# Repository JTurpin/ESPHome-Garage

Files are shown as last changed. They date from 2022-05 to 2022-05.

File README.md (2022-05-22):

# ESPHome Based Garage Monitor

## Introduction
I built this circuit board to monitor my garage as well as control the garage door opener. This board is capable of reading door state through a switch, controlling the door, and using a BME680 to measure, temperature, humidity, volatile organic compounds (combustible gasses), and carbon dioxide.

## Hardware
Custom PCB created in Eagle CAD. I had these run at [seeedstudio-fusion](https://www.seeedstudio.com/fusion_pcb.html). The boards have been tested and are currently functioning in my garage.

## Interfacing with the garage door opener
There are inputs and outputs to read and control up to two doors. The ```DoorX-In``` are a simple digital read. I use magnetic reed switches that are normally open for this. They can be had cheaply as many alarm system used the for door and window sensors like [this](https://www.amazon.com/VictorsHome-Magnetic-Surface-Adhesive-Security/dp/B094XJ7K8K).

To controll the door simply run a 2 conductor wire from the ```DoorX`` screw terminals to the same terminals that the wall switch mounted inside the garage is connected to.

## Home Assistant Configuration
ESPHome needs to be installed and functioning:
1) Click on ```+ NEW DEVICE```
1) Click ```Continue```
2) Give it a name, I chose ```garage-monitor```
3) Select ```Pick specific board``` and ```Wemos D1 and Wemos D1 mini```
4) Select ```Skip```
5) Find the device and click ```EDIT```
6) Paste in the [yaml](ESPHome/garage-sensor.yaml) file and edit the proper wifi setting.
  
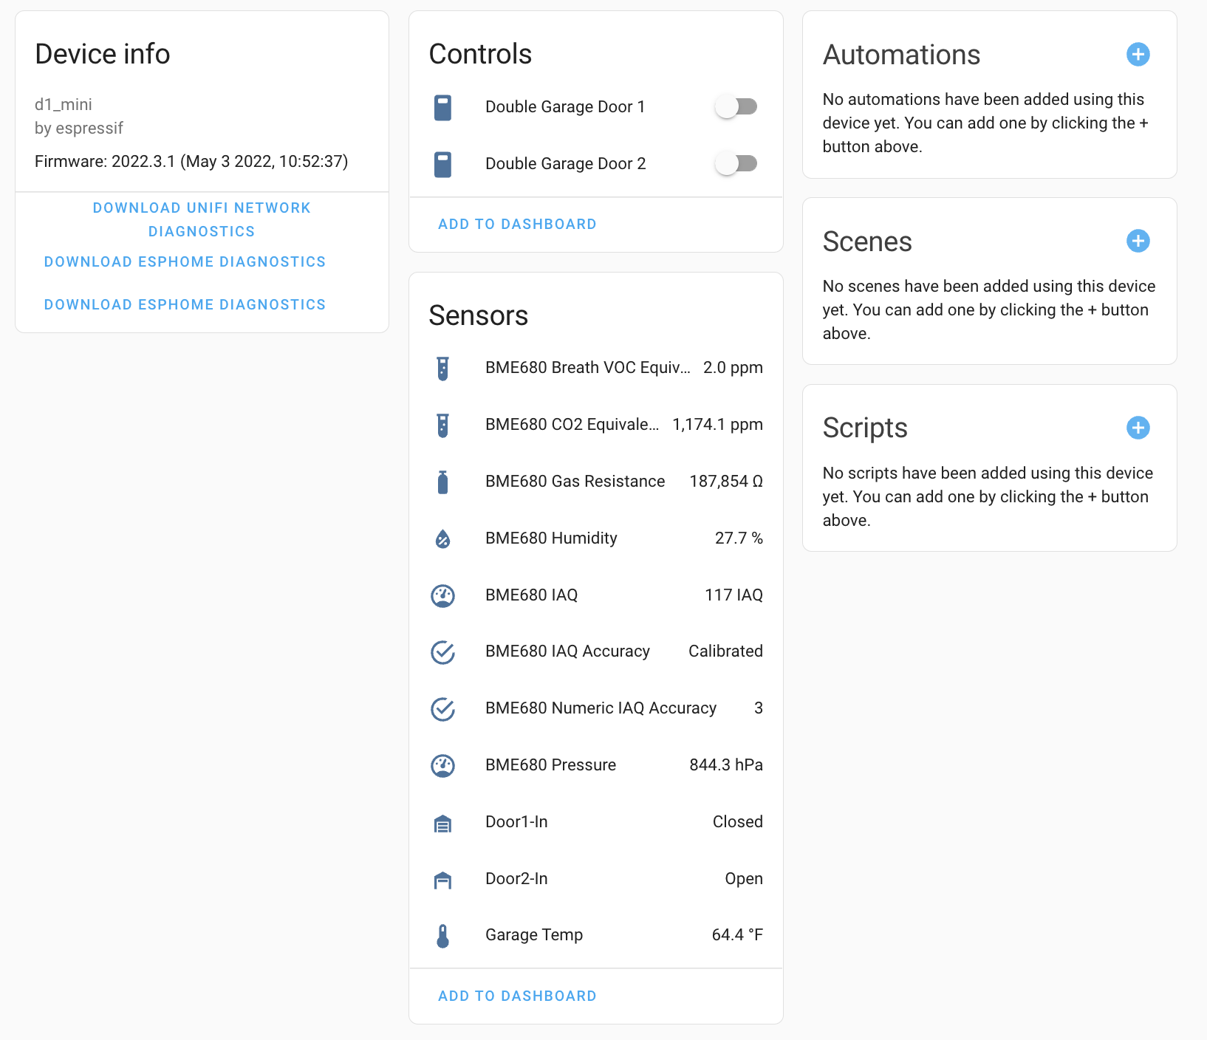
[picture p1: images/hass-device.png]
Home Assistant device view


## Automations
I use NodeRed to automate many aspects of my smart home. Here are a couple related to my garage to get you going.
- Notify via pushover if the garage door is open for 15 minutes [json](NodeRed%20Flows/notify-door-open.json) NodeRed
- Quick reset the output on the "button push" (There is probably a better way to do this but I found this to be effective) [json](NodeRed%20Flows/quick-trigger.json) NodeRed

## To Do...
There's two WS2812b on the board that I haven't found a use for yet, they could be used for a number of things though. examples:
- Countdown timer until autmoated shut of garage door
- Gauge estimates like [this](images/lovelace_gauge_segments.png) for Temp, VOC, Humidity, CO2.
- etc

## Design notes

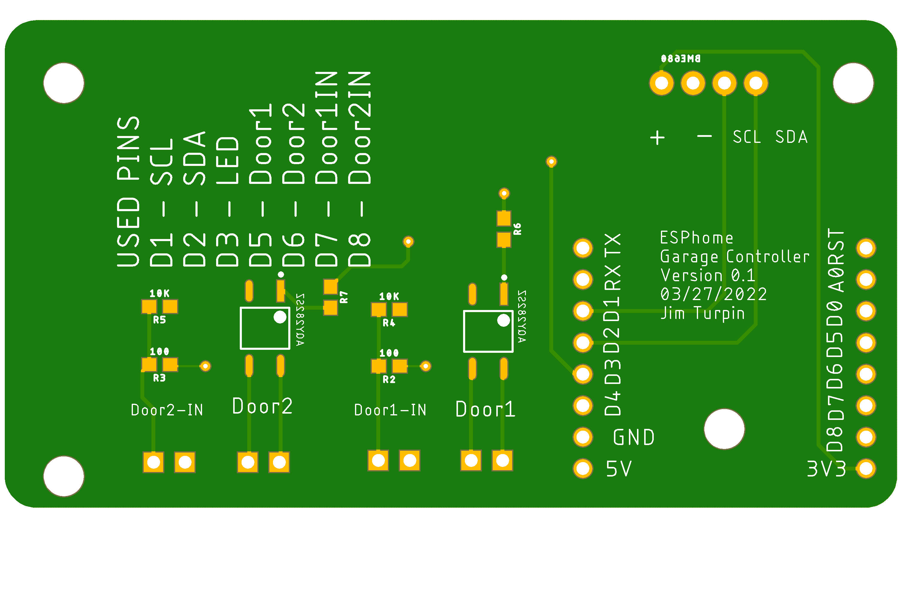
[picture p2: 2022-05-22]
images/PCB-bottom.png

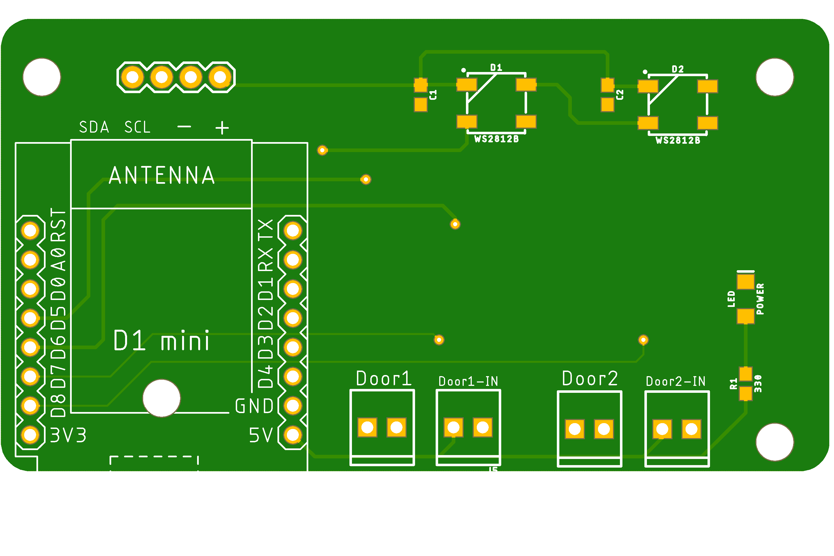
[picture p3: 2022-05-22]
images/PCB-top.png

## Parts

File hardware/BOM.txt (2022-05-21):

Partlist exported from Eagle

Part   Value         Device                               Package             Description                                                                                                     AMBIENT_TEMPERATURE_RANGE_HIGH AMBIENT_TEMPERATURE_RANGE_LOW AUTOMOTIVE CAPACITANCE CENTROID_NOT_SPECIFIED DATASHEET                                                          DEVICE_CLASS_L1   DEVICE_CLASS_L2 DEVICE_CLASS_L3    DIGIKEY_DESCRIPTION          DIGIKEY_PART_NUMBER FOOTPRINT_PARAMETERS_1                                                                                                                                                                                                                                                                                                                                                                                                                                                                                                                                                                                                                                                                                                                                                                                                                                                                                                                                                                                                                                                                                                                                                                                                                                                                                                                                                                                                                                                                                                                                                                                                                                                                                                                                                                                                                                                                                                                                                                                                                                                                                                                                                                                                                                                                                                                                                                                                                                                                                                                                                                                                                                                                                FOOTPRINT_PARAMETERS_2                                                                                                                                                                                                                                                                                                                                                                                                                                                                                                                                                                                                                                                                                                                                                                                                                                                                                                                                                                                                                                                                                                                                                                                                                                                                                                                                                                                                                                                                                                                                                                                                                                                                                                                                                                                                                                                                                                                                                                                                                                                                                                                                                                                                                                                                                                                                                                                                                                                                                                                                                                                                                                                                                FOOTPRINT_PARAMETERS_3                                                                                                                                                                                                                                                                                                                                                                                                                                                                                                                                                                                                                                                                                                                                                                                                                                                                                                                                                                                                                                                                                                                                                                                                                                                                                                                                                                                                                                                                                                                                                                                                                                                                                                                                                                                                                                                                                                                                                                                                                                                                                                                                                                                                                                                                                                                                                                                                                                                                                                                                                                                                                                                                                FOOTPRINT_VARIANT_NAME_0  FOOTPRINT_VARIANT_NAME_1 FOOTPRINT_VARIANT_NAME_2 FOOTPRINT_VARIANT_NAME_3 HEIGHT INPUT_CURRENT IPC_LAND_PATTERN_NAME ISOLATION_VOLTAGE LEAD_FREE MAX_JUNCTION_TEMP MF    MFG_PACKAGE_IDENT MFG_PACKAGE_IDENT_DATE MFG_PACKAGE_IDENT_REV MOUSER_DESCRIPTION                                          MOUSER_PART_NUMBER MPN        NUMBER_OF_CONTACTS ON_STATE_RESISTANCE OUTPUT_CURRENT OUTPUT_VOLTAGE PACKAGE PREFIX PROD_ID    ROHS STANDOFF_HEIGHT TEMPERATURE_RANGE_HIGH TEMPERATURE_RANGE_LOW THROW_CONFIGURATION VALUE   VERIFICATION_VERSION
C1     15pF          15PF-0603-50V-5%                     0603                15pF ceramic capacitors                                                                                                                                                                                                                                                                                                                                                                                                                                                                                                                                                                                                                                                                                                                                                                                                                                                                                                                                                                                                                                                                                                                                                                                                                                                                                                                                                                                                                                                                                                                                                                                                                                                                                                                                                                                                                                                                                                                                                                                                                                                                                                                                                                                                                                                                                                                                                                                                                                                                                                                                                                                                                                                                                                                                                                                                                                                                                                                                                                                                                                                                                                                                                                                                                                                                                                                                                                                                                                                                                                                                                                                                                                                                                                                                                                                                                                                                                                                                                                                                                                                                                                                                                                                                                                                                                                                                                                                                                                                                                                                                                                                                                                                                                                                                                                                                                                                                                                                                                                                                                                                                                                                                                                                                                                                                                                                                                                                                                                                                                                                                                                                                                                                                                                                                                                                                                                                                                                                                                                                                                                                                                                                                                                                                                                                                                                                                                                                                                                                                                                                                                                                                                                                                                                                                                                                                                                                                                                                                                                                                                                                                                                                                                                                                                                                                                                                                                                                                                                                                                                                                                                                                                                                                                                                                                                                                                                                                                                                                                                                                                                                                                                                                                                                                                                                                                                                                                                                                                                                                                                                                                                                                                                                                                                                                                                                                                                                                                                                                                CAP-07881                                                                                        15pF                        
C2     15pF          15PF-0603-50V-5%                     0603                15pF ceramic capacitors                                                                                                                                                                                                                                                                                                                                                                                                                                                                                                                                                                                                                                                                                                                                                                                                                                                                                                                                                                                                                                                                                                                                                                                                                                                                                                                                                                                                                                                                                                                                                                                                                                                                                                                                                                                                                                                                                                                                                                                                                                                                                                                                                                                                                                                                                                                                                                                                                                                                                                                                                                                                                                                                                                                                                                                                                                                                                                                                                                                                                                                                                                                                                                                                                                                                                                                                                                                                                                                                                                                                                                                                                                                                                                                                                                                                                                                                                                                                                                                                                                                                                                                                                                                                                                                                                                                                                                                                                                                                                                                                                                                                                                                                                                                                                                                                                                                                                                                                                                                                                                                                                                                                                                                                                                                                                                                                                                                                                                                                                                                                                                                                                                                                                                                                                                                                                                                                                                                                                                                                                                                                                                                                                                                                                                                                                                                                                                                                                                                                                                                                                                                                                                                                                                                                                                                                                                                                                                                                                                                                                                                                                                                                                                                                                                                                                                                                                                                                                                                                                                                                                                                                                                                                                                                                                                                                                                                                                                                                                                                                                                                                                                                                                                                                                                                                                                                                                                                                                                                                                                                                                                                                                                                                                                                                                                                                                                                                                                                                                CAP-07881                                                                                        15pF
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

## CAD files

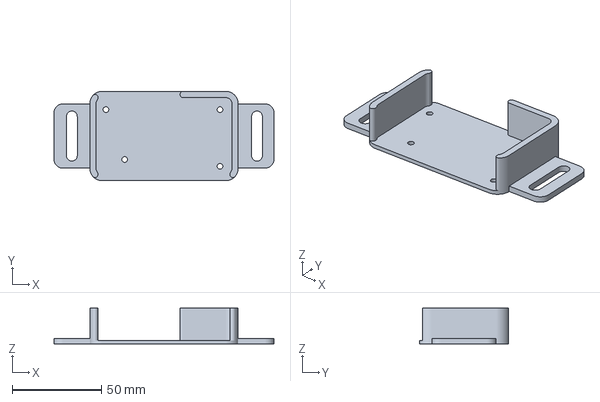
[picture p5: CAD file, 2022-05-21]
hardware/STL/ESPHome-Garage.3mf
123.0 x 50.0 x 20.0 mm

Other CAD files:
hardware/STL/ESPHome-Garage.f3d
hardware/STL/ESPHome-Garage.stl

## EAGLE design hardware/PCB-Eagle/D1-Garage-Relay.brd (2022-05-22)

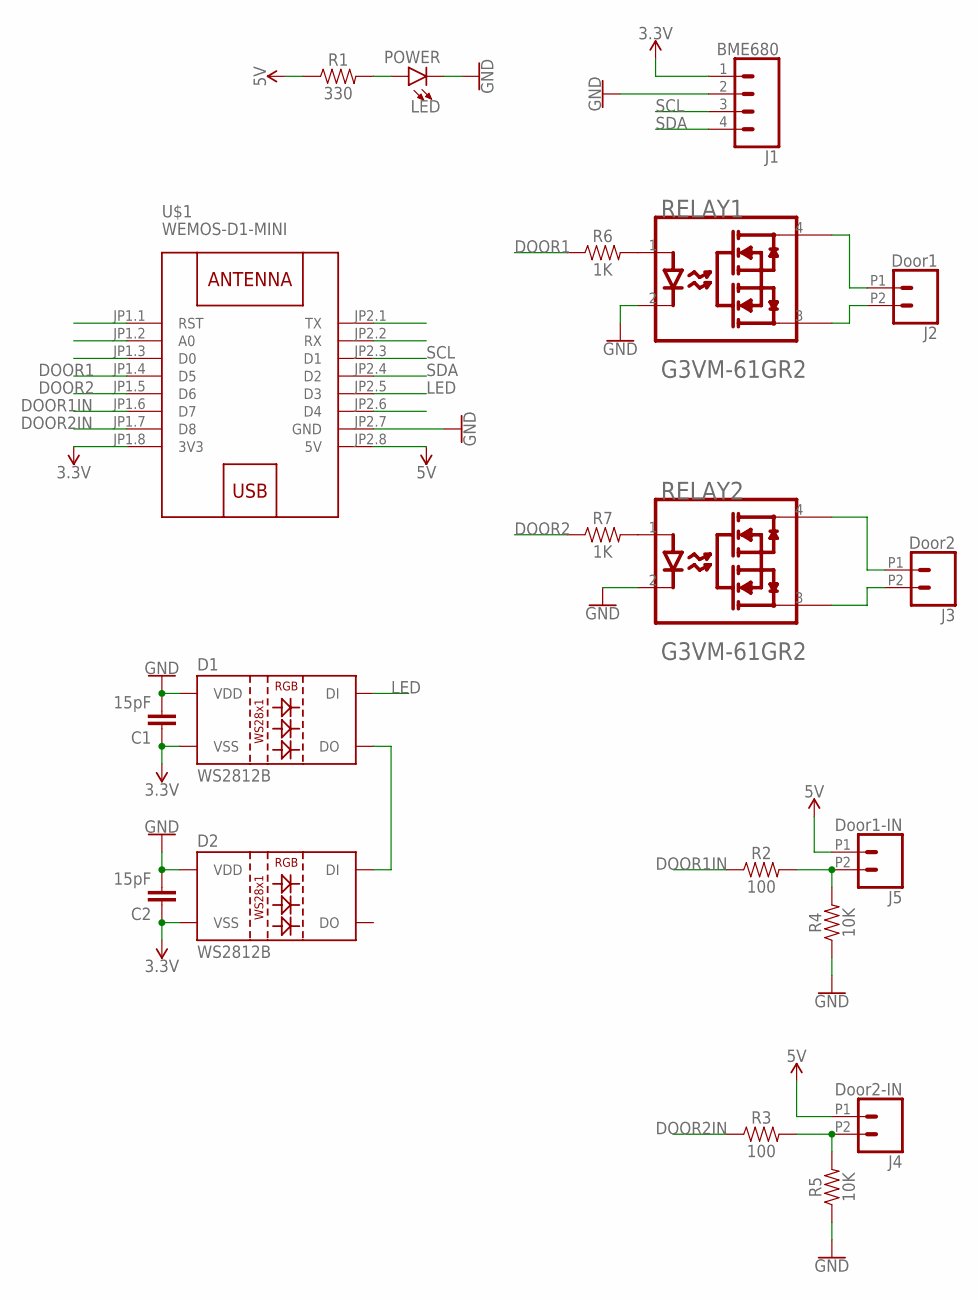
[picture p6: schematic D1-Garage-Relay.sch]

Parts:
C1, C2: 15pF; 0603
D1, D2: WS2812B
J1: BME680; 1X04
J2: Door1; 1X02_2.54_SCREWTERM
J3: Door2; 1X02_2.54_SCREWTERM
J4: Door2-IN; 1X02_2.54_SCREWTERM
J5: Door1-IN; 1X02_2.54_SCREWTERM
LED: POWER; LED-1206
R1: 330; 0603
R2, R3: 100; 0603
R4, R5: 10K; 0603
R6, R7: 1K; 0603
RELAY1, RELAY2: AQY282SZ; OMRON_G3VM-61GR2_3
U$1: WEMOS-D1-MINI

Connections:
3.3V: C1.1, C2.1, D1.3 (VSS), D2.3 (VSS), J1.1, U$1.JP1.8 (3V3)
5V: J4.P1 (1), J5.P1 (1), R1.1, U$1.JP2.8 (5V)
DOOR1: R6.1, U$1.JP1.4 (D5)
DOOR1IN: R2.1, U$1.JP1.6 (D7)
DOOR2: R7.1, U$1.JP1.5 (D6)
DOOR2IN: R3.1, U$1.JP1.7 (D8)
GND: C1.2, C2.2, D1.1 (VDD), D2.1 (VDD), J1.2, LED.C, R4.1, R5.1, RELAY1.2 (CATHODE), RELAY2.2 (CATHODE), U$1.JP2.7 (GND)
LED: D1.4 (DI), U$1.JP2.5 (D3)
unnamed: J2.P2 (2), RELAY1.3 (1_DRAIN)
unnamed: J3.P2 (2), RELAY2.3 (1_DRAIN)
unnamed: J2.P1 (1), RELAY1.4 (2_DRAIN)
unnamed: R6.2, RELAY1.1 (ANODE)
unnamed: J3.P1 (1), RELAY2.4 (2_DRAIN)
unnamed: R7.2, RELAY2.1 (ANODE)
unnamed: LED.A, R1.2
unnamed: J5.P2 (2), R2.2, R4.2
unnamed: J4.P2 (2), R3.2, R5.2
unnamed: D1.2 (DO), D2.4 (DI)
SCL: J1.3, U$1.JP2.3 (D1)
SDA: J1.4, U$1.JP2.4 (D2)

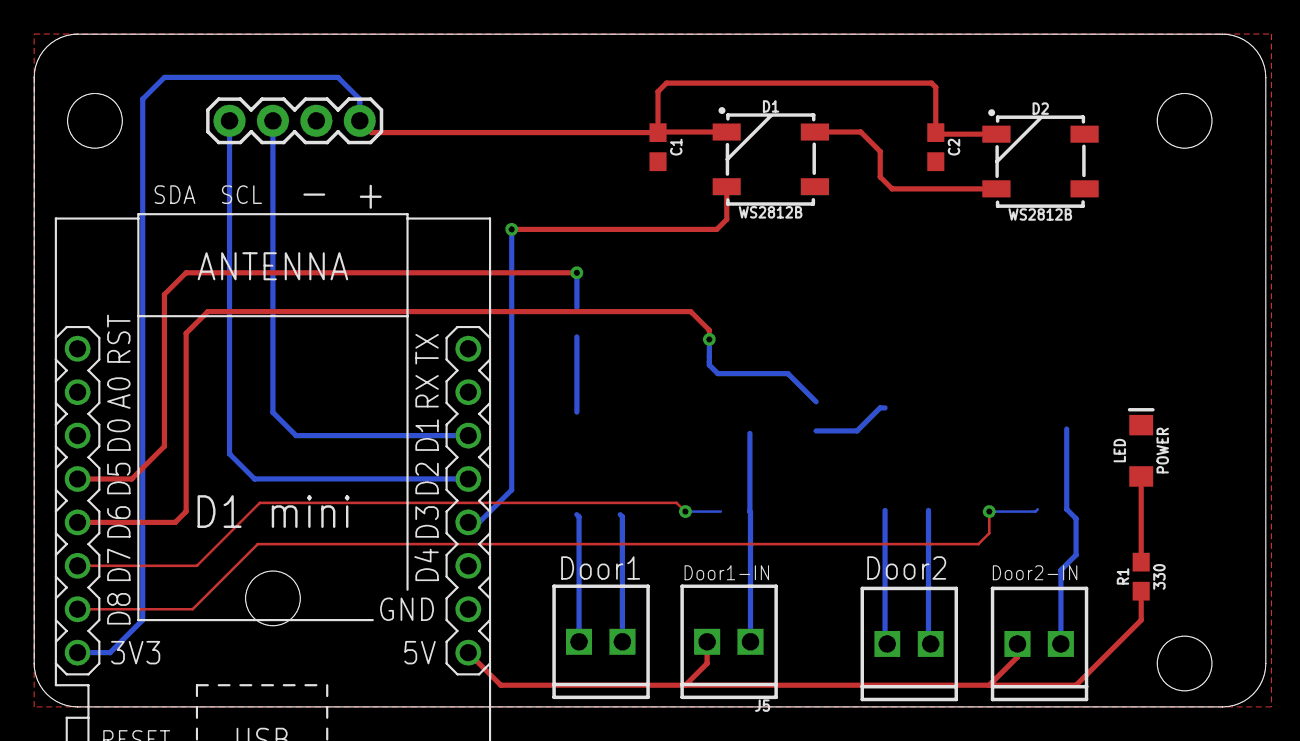
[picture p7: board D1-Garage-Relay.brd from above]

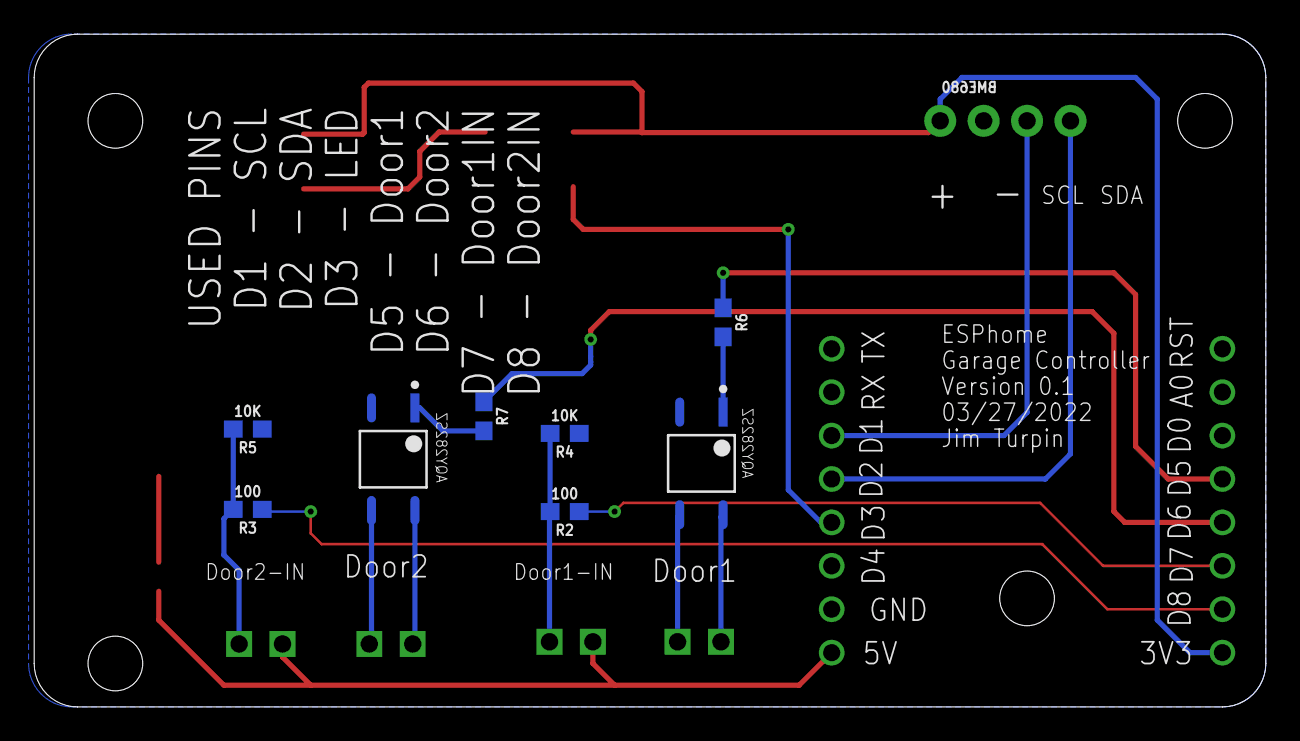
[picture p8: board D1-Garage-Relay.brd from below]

Board: 2 copper layers, 72.1 x 39.4 mm, 20 parts (8 on the bottom side), 20 nets.

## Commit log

2022-05-21 adding images of the PCB
2022-05-22 adjusted bottom layer to accomodate documentation
    [D1-Garage-Relay.brd]

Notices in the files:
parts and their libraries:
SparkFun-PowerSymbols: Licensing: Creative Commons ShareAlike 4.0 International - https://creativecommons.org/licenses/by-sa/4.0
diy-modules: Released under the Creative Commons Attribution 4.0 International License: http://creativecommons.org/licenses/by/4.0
